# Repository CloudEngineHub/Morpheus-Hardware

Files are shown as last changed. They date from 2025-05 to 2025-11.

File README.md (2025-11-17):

<div align="center">
<h2>Morpheus: A Neural-driven Animatronic Face with<br>
  Hybrid Actuation and Diverse Emotion Control</h2>

  **RSS 2025**
  
<h2>Hardware Design</h2>

**Zongzheng Zhang**<sup>1,2*</sup> · **Jiawen Yang**<sup>1*</sup> · [**Ziqiao Peng**](https://ziqiaopeng.github.io/)<sup>1</sup> ·<br>
**Meng Yang**<sup>4</sup> · [**Jianzhu Ma**](https://majianzhu.com/)<sup>1</sup>, **Lin Cheng**<sup>5</sup> · [**Huazhe Xu**](http://hxu.rocks/)<sup>3</sup> . [**Hang Zhao**](https://hangzhaomit.github.io/)<sup>3</sup> and [**Hao Zhao**](https://sites.google.com/view/fromandto/)<sup>1,2</sup><br>

<sup>1</sup> Institute for AI Industry Research (AIR), Tsinghua University, <sup>2</sup> Beijing Academy of Artificial Intelligence (BAAI),<br>
<sup>3</sup> Institute for Interdisciplinary Information Sciences(IIIS), Tsinghua University, <br>
<sup>4</sup> MGI Tech, Shenzhen, China, <sup>5</sup> Beihang University<br>
<sub>(* indicates equal contribution)</sub><br>
[**RSS official**](https://roboticsconference.org/program/papers/80/) | [**Project Page**](https://jiawenyang-ch.github.io/Morpheus-Hardware-Design/) | [**arXiv**](https://arxiv.org/abs/2507.16645) | [**Hardware**](https://github.com/ZZongzheng0918/Morpheus-Hardware) | [**Software**](https://github.com/ZZongzheng0918/Morpheus-Software)
</div>
<div align="center">
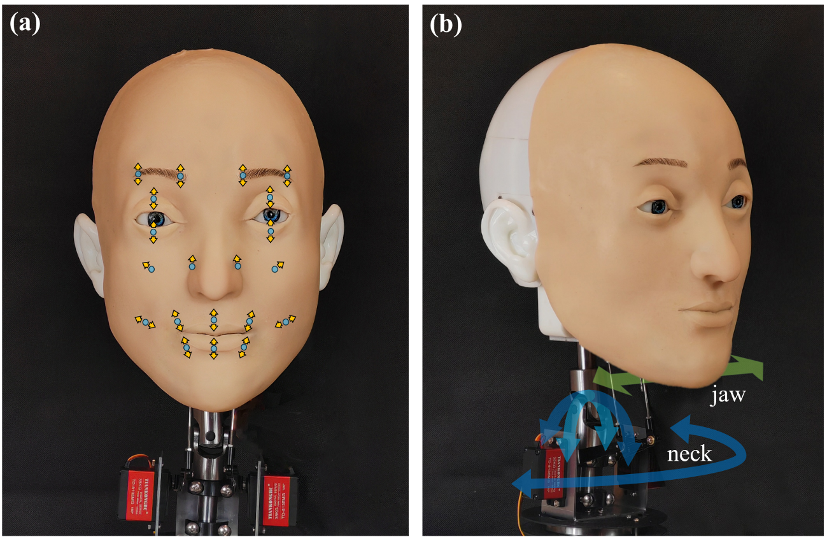
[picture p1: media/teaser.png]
teaser_1
  
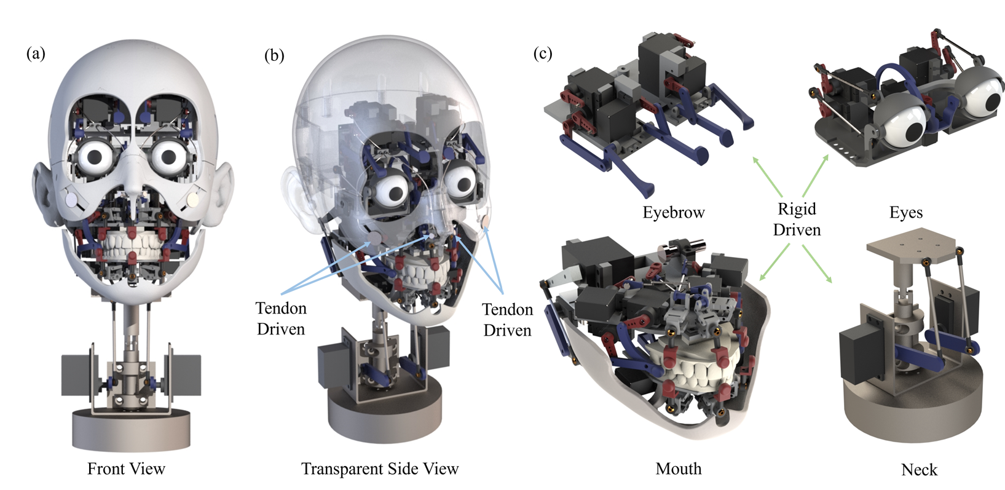
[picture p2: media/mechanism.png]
  
</div>

## Catalog
- [CAD model Download](#cAD_model-Download)
- [Bill of Materials](#bill-of-materials)
- [File content](#file-content)
- [Building Instructions](#building-instructions)
- [Silicone Face](#silicon-face)
- [License and Acknowledgements](#license-and-acknowledgements)
- [Citation](#citation)

## CAD model Download
Due to the large size of the CAD model files, they are hosted on Google Drive instead of being uploaded directly to GitHub. You can download the entire CAD model via the following link:

[Download CAD Model Files](https://drive.google.com/drive/folders/1n12V-EUoFsY6ys1dDMhCXVMRPuU5FeQE?usp=drive_link)

Please ensure you have **SolidWorks 2020 or later** installed to open and edit these files.

## Bill of Materials
All costs are listed in USD.
<table>
  <thead>
    <tr>
      <th>Item</th>
      <th>Quantity</th>
      <th>Cost per Item</th>
      <th>Total Cost</th>
      <th>Note</th>
    </tr>
  </thead>
  <tbody>
    <tr>
      <td>Integy RC GuoHua A0090 9g Metal Gear Digital Micro Servo 6kg</td>
      <td>29</td>
      <td>4.06</td>
      <td>117.74</td>
      <td><a href="https://www.amazon.com/Integy-Model-C30371-GuoHua-Digital/dp/B09CXFTQD5">Purchase Link</a></td>
    </tr>
    <tr>
      <td>RC Spare Part Compatible with KS3518 Rc Car Waterproof Metal Digital Servo High Torque Mechanical Arm Hand Metal Servo Motor</td>
      <td>4</td>
      <td>59.35</td>
      <td>237.4</td>
      <td><a href="https://www.amazon.com/Compatible-KS3518-Waterproof-Digital-Mechanical/dp/B0F5M32RWP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">Purchase Link</a></td>
    </tr>
    <tr>
      <td>10pcs 3-Pin 30cm Servo Extension Cable Cord Female to Male Lead Wire Connector JR for RC Car Airplanes Remote Control-30mm</td>
      <td>33</td>
      <td>7.99</td>
      <td>263.67</td>
      <td><a href="https://www.amazon.com/ACEIRMC-Extension-Connector-Airplanes-Control/dp/B0CQ4QKDF4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">Purchase Link</a></td>
    </tr>
    <tr>
      <td>550PCS M3 Screw Kit</td>
      <td>4</td>
      <td>9.99</td>
      <td>39.96</td>
      <td><a href="https://www.amazon.com/Bemaka-550PCS-Washers-Assortment-Stainless/dp/B0D5CSSYGH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">Purchase Link</a></td>
    </tr>
    <tr>
      <td>Replacement Part For M3 Adjustable Push Rod & Ball Joint Linkage Set Assembly Servo Connecting Rod Stainless Steel For RC Aircraft Boat Part - (Color: 35mm)</td>
      <td>4</td>
      <td>13.99</td>
      <td>55.96</td>
      <td><a href="https://www.amazon.com/dp/B09B3RCDB3/ref=twister_B09B3RLR5K?_encoding=UTF8&th=1">Purchase Link</a></td>
    </tr>
    <tr>
      <td>5/10sets M2 304 Stainless Steel Leather Bag Belt Photo Scrapbook Album Book Post Binding Screw Screw Rivet Metal Screws</td>
      <td>20</td>
      <td>9.66</td>
      <td>193.2</td>
      <td><a href="https://www.amazon.com/YUYUDEHM-Chicago-Assorted-Leather-Bookbinding/dp/B0DGQ5NVW1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">Purchase Link</a></td>
    <tr>
      <td>12Pack Vgoohobby Metal M3 Tie Rod End Ball Holder RC Joint Link Ball Head Holder CW Compatible with HSP Traxxas HPI Axial Redcat Racing 1/10 RC Car Truck Buggy Crawler</td>
      <td>6</td>
      <td>12.99</td>
      <td>77.94</td>
      <td><a href="https://www.amazon.com/12Pack-Vgoohobby-Compatible-Traxxas-Crawler/dp/B0BHF2WG1V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">Purchase Link</a></td>
    </tr>
    <tr>
      <td>2Pcs Aluminum 1.75inch 25T Servo Arm Horn Long Steering Servo Arms Compatible Futaba Savox Xcore HL HSP HD Power Rc Servos for RC Airplanes RC Plane Crawler Car</td>
      <td>1</td>
      <td>9.99</td>
      <td>9.94</td>
      <td><a href="https://www.amazon.com/Aluminum-1-75inch-Steering-Compatible-Airplanes/dp/B0DZBCJXHX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">Purchase Link</a></td>
    </tr>
    <tr>
      <td>LML9B 9mm Linear Rail Mini Bearing Steel Rail Slide Rail+ Slide Block Variety Length (55mm)</td>
      <td>1</td>
      <td>11.62</td>
      <td>11.62</td>
      <td><a href="https://www.amazon.com/LML9B-Linear-Bearing-Variety-Length/dp/B07GQJ9LT8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">Purchase Link</a></td>
    </tr>
    <tr>
      <td>7pcs Realistic Fake Tongue, Magic Tricks Accessories, Halloween Pranking False Tongue Horrific Tongue Prop Tricks Tongue Toys (009)</td>
      <td>1</td>
      <td>8.55</td>
      <td>8.55</td>
      <td><a href="https://www.amazon.com/Realistic-Accessories-Halloween-Pranking-Horrific/dp/B096V99JD5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">Purchase Link</a></td>
    </tr>
    <tr>
      <td>2 Pcs 8mm to 8mm Universal Joint Shaft Coupling with Screws for Motor</td>
      <td>1</td>
      <td>11.99</td>
      <td>11.99</td>
      <td><a href="https://www.amazon.com/Befenybay-Universal-Joint-Coupling-Screws/dp/B07V9NTQLH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">Purchase Link</a></td>
    </tr>
    </tr>
    <tr>
      <td>CanaKit Raspberry Pi 5 Starter Kit PRO - Turbine Black (128GB Edition) (8GB RAM)</td>
      <td>1</td>
      <td>159.99</td>
      <td>159.99</td>
      <td><a href="https://www.amazon.com/CanaKit-Raspberry-Starter-Kit-PRO/dp/B0CRSNCJ6Y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">Purchase Link</a></td>
    </tr>
    <tr>
      <td colspan="3"><b>Total</b></td>
      <td colspan="2"><b>1619.14</b></td>
    </tr>
  </tbody>
</table>

## File content
**Note: This model is compatible with SolidWorks 2020 and later versions.**
```plaintext
CAD_model
├── full_assembly.SLDASM
├── cheek_face_slave_part_mirror.SLDPRT
├── cheek_facial_slave_part_mirror.SLDPRT
├── cheek_line.SLDPRT
├── ks3518.SLDPRT
├── L.SLDPRT
├── nose_line.SLDPRT
├── nose_mirror_line.SLDPRT
├── nose_mirror_slave_part.SLDPRT
├── nose_slave_part.SLDPRT
├── OT.SLDPRT
├── OT_mirror.SLDPRT
├── Raspberry_Pi_(computer_science).SLDPRT
├── shell_back_of_the_head.SLDPRT
├── shell_carapace.SLDPRT
├── shell_Face_Bone_Connectors.SLDPRT
├── shell_Face_Bone_Connectors_mirror.SLDPRT
├── shell_facial_bones.SLDPRT
├── shell_left_ears.SLDPRT
├── shell_right_ears.SLDPRT
├── shell_skin_face.SLDPRT
├── studs.SLDPRT
├── studs_60.SLDPRT
├── "eye"
│   ├── eye.SLDASM
│   ├── eye_Balls_for_head_pulls.SLDPRT
│   ├── eye_bassinet.SLDPRT
│   ├── eye_comb.SLDPRT
│   ├── eye_crank_handle.SLDPRT
│   ├── eye_Eyeball_mounts.SLDPRT
│   └── eye_Eyelid_mounting_stubs.SLDPRT
│   ├── eye_lower_eyelid_of_the_right_eye.SLDPRT
│   ├── eye_lower_eyelid_of_the_right_eye_mirror.SLDPRT
│   ├── eye_m_shaped_board.SLDPRT
│   ├── eye_mounted_version.SLDPRT
│   ├── eye_pupil.SLDPRT
│   ├── eye_Shanks_for_Ball_Tie_Rods.SLDPRT
│   ├── eye_upper_eyelid_of_the_right_eye.SLDPRT
│   ├── eye_upper_eyelid_of_the_right_eye_mirror.SLDPRT
│   ├── eye_y_connector.SLDPRT
├── "eyebrow"
│   ├── EYEBROW.SLDASM
│   ├── eyebrow_brow center motor mounting bracket.SLDPRT
│   ├── eyebrow_brow center pendulum.SLDPRT
│   ├── eyebrow_connected model aircraft regulator.SLDPRT
│   ├── eyebrow_crank v4.SLDPRT
│   ├── eyebrow_eyebrow peak rocker 1.SLDPRT
│   ├── eyebrow_eyebrow peak rocker.SLDPRT
│   ├── eyebrow_GUOHUAA0090.SLDPRT
│   ├── eyebrow_Installation platform.SLDPRT
│   ├── eyebrow_mirror brow center motor mounting bracket.SLDPRT
│   ├── eyebrow_mirror brow center pendulum.SLDPRT
│   ├── eyebrow_mirror eyebrow peak rocker 1.SLDPRT
│   ├── eyebrow_short brow joystick.SLDPRT
├── "mouth"
│   ├── mouth assembly.SLDASM
│   ├── mouth_aluminum rocker arm.SLDPRT
│   ├── mouth_ball of spherical hinge.SLDPRT
│   ├── mouth_baseplate for teeth.SLDPRT
│   ├── mouth_baseplate.SLDPRT
│   ├── mouth_bearing cap.SLDPRT
│   ├── mouth_connector for OT head.SLDPRT
│   ├── mouth_connector for OT head_4mm medium.SLDPRT
│   ├── mouth_connector for OT head_4mmlong.SLDPRT
│   ├── mouth_convex iron wire.SLDPRT
│   ├── mouth_crank.SLDPRT
│   ├── mouth_fourth-generation jaw.SLDPRT
│   ├── mouth_gear.SLDPRT
│   ├── mouth_GUOHUAA0090.SLDPRT
│   ├── mouth_iron wire 30mm.SLDPRT
│   ├── mouth_iron wire_below middle.SLDPRT
│   ├── mouth_iron wire_freedom20mm.SLDPRT
│   ├── mouth_iron wire_freedom30mm.SLDPRT
│   ├── mouth_iron wire_upper middle.SLDPRT
│   ├── mouth_jaw five-bar mechanism_long.SLDPRT
│   ├── mouth_jaw five-bar mechanism_short.SLDPRT
│   ├── mouth_ks3518.SLDPRT
│   ├── mouth_lip connecting rod.SLDPRT
│   ├── mouth_lip six-bar mechanism_4mm crossbar.SLDPRT
│   ├── mouth_lip six-bar mechanism_8mm crossbar.SLDPRT
│   ├── mouth_lower teeth.SLDPRT
│   ├── mouth_metal ball of spherical hinge.SLDPRT
│   ├── mouth_MG90S.SLDPRT
│   ├── mouth_MGN7C_slider.SLDPRT
│   ├── mouth_MGR7_slider rail.SLDPRT
│   ├── mouth_mirror_motor mounting platform for smiling six-bar mechanism.SLDPRT
│   ├── mouth_mirror_oblique crank extension rod.SLDPRT
│   ├── mouth_mirror_smiling five-bar mechanism_below.SLDPRT
│   ├── mouth_motor mounting platform for smiling six-bar mechanism.SLDPRT
│   ├── mouth_mounting platform for upper lip connecting rod.SLDPRT
│   ├── mouth_oblique crank extension rod.SLDPRT
│   ├── mouth_OT head.SLDPRT
│   ├── mouth_perforated crank.SLDPRT
│   ├── mouth_rack.SLDPRT
│   ├── mouth_self-made ball hinge rod for the lower teeth.SLDPRT
│   ├── mouth_shaft flange.SLDPRT
│   ├── mouth_six-bar mechanism_above_short.SLDPRT
│   ├── mouth_six-bar mechanism_below_short.SLDPRT
│   ├── mouth_six-bar mechanism_with spherical hinge.SLDPRT
│   ├── mouth_slide rail mounting plate.SLDPRT
│   ├── mouth_smiling five-bar mechanism_above.SLDPRT
│   ├── mouth_smiling five-bar mechanism_below.SLDPRT
│   ├── mouth_smiling six-bar mechanism_above.SLDPRT
│   ├── mouth_smiling six-bar mechanism_below.SLDPRT
│   ├── mouth_spherical hinge.SLDPRT
│   ├── mouth_threaded pin.SLDPRT
│   ├── mouth_threaded rod of spherical hinge.SLDPRT
│   ├── mouth_tongue connecting rod.SLDPRT
│   ├── mouth_tongue connecting rod_long.SLDPRT
│   ├── mouth_tongue pulling rod.SLDPRT
│   ├── mouth_tongue tray.SLDPRT
│   ├── mouth_upper lip connection point.SLDPRT
│   ├── mouth_upper teeth.SLDPRT
└── "neck"
    ├── neck.SLDASM
    ├── neck_Axis_positioning_tools.SLDPRT
    ├── neck_ball.SLDPRT
    ├── neck_ball_hinge.SLDPRT
    ├── neck_crosshairs.SLDPRT
    ├── neck_extension_arm.SLDPRT
    ├── neck_Installation_of_sheet_metal.SLDPRT
    ├── neck_Parallel_platforms.SLDPRT
    ├── neck_pole.SLDPRT
    ├── neck_principal_axis.SLDPRT
    ├── neck_transition_part.SLDPRT
    ├── neck_universal_joint.SLDPRT
    ├── neck_Upper_shaft.SLDPRT
    └── neck_y_axis_platform.SLDPRT
```

## Building Instructions

### Screw guide

- **Screw A**: M2.5 × 8 mm (Self-tapping) 
- **Screw B**: M3 × 10 mm (Self-tapping) 
- **Screw C**: &#8960;3 (mating screw)  
- **Screw D**: M3  
- **Screw E**: M2 × 10 mm  

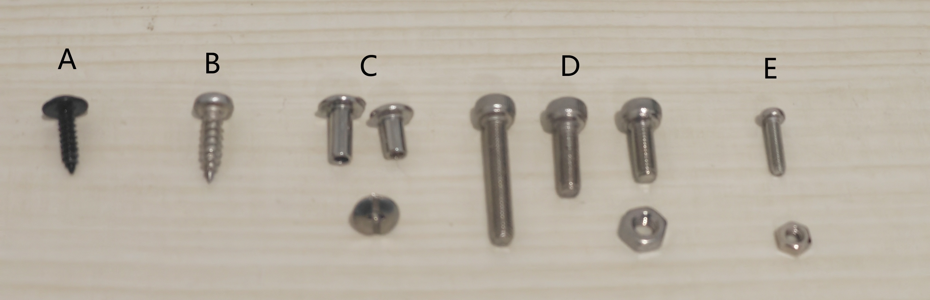
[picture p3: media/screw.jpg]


### Neck module
The *neck_Installation_of_sheet_metal* is installed on the *neck_y_axis_platform* using 4 pairs of screws.

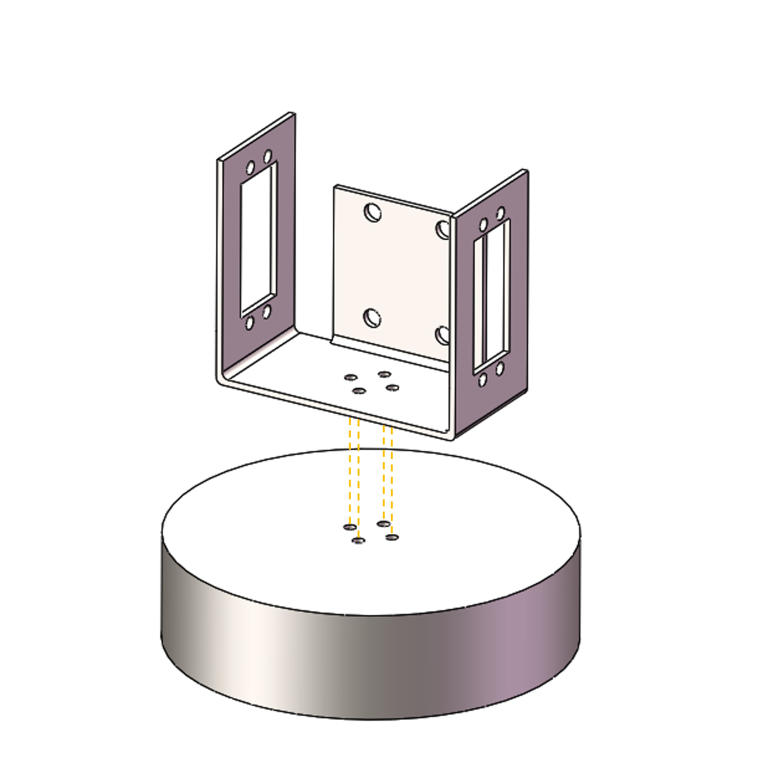
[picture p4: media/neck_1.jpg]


Two *ks3518* servo motors are installed on the *neck_Installation_of_sheet_metal* on both sides.

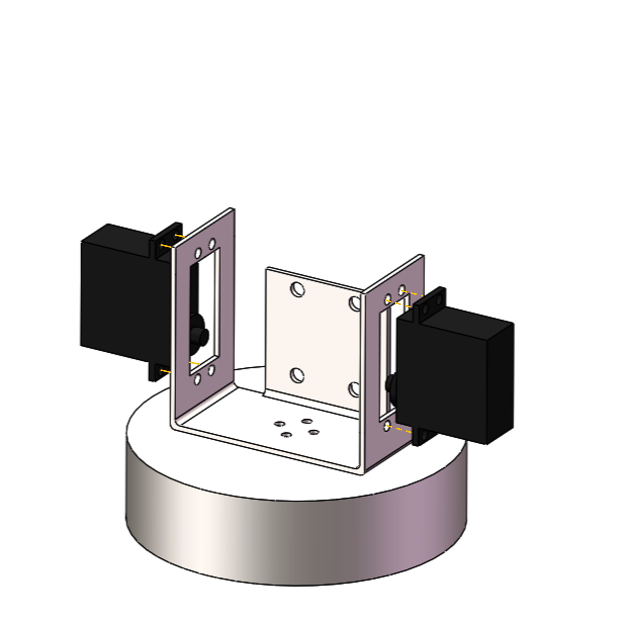
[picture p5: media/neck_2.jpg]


The *neck_extension_arm* is installed on each *ks3518* servo motor to deliver power.

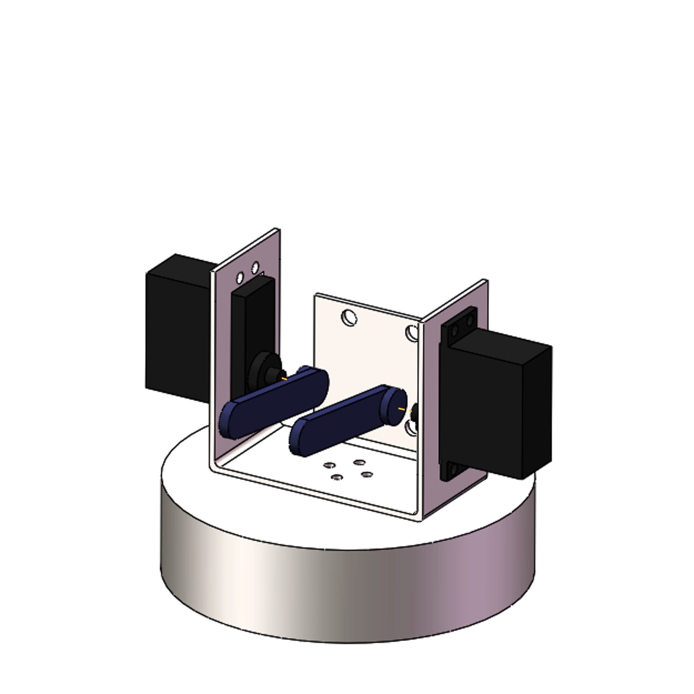
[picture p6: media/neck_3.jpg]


The *neck_principal_axis* is a section of plain shaft which stands on the *neck_Installation_of_sheet_metal*.

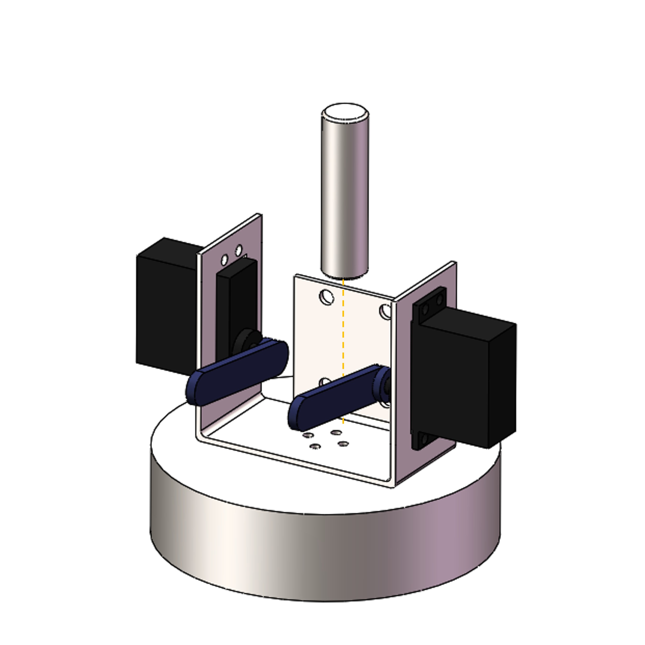
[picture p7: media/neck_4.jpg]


Two *neck_Axis_positioning_tools* are deployed to fix the *neck_principal_axis*.

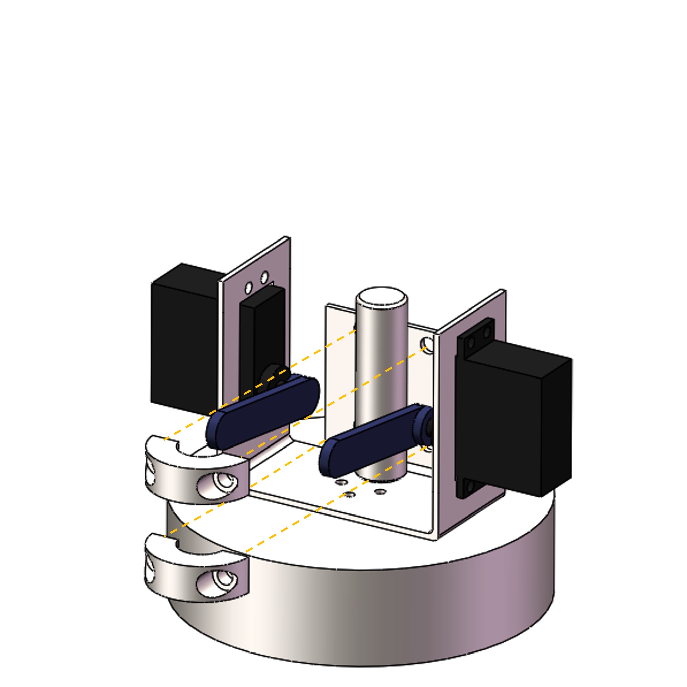
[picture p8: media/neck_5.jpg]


The universal joint is assembled on the upper end of the shaft.

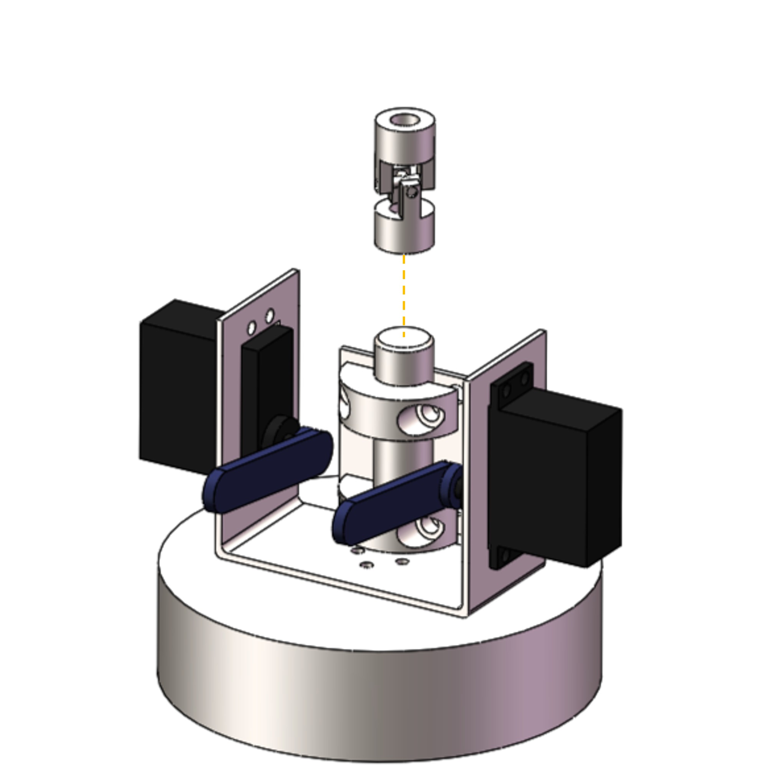
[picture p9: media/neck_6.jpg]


The *neck_Parallel_platforms* is attached with the universal joint with the *neck_Upper_shaft*. 

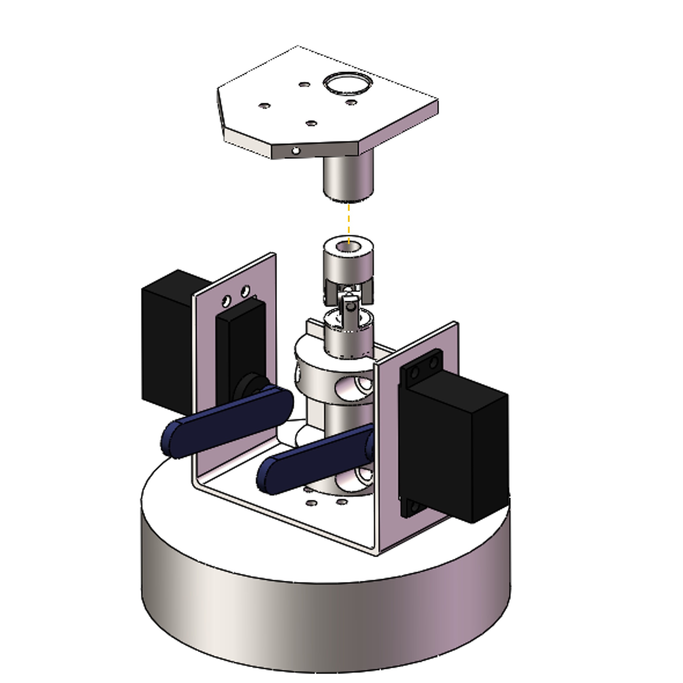
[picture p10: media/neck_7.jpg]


Two rod linkages connect the *neck_Parallel_platforms* and the *neck_extension_arm*s.

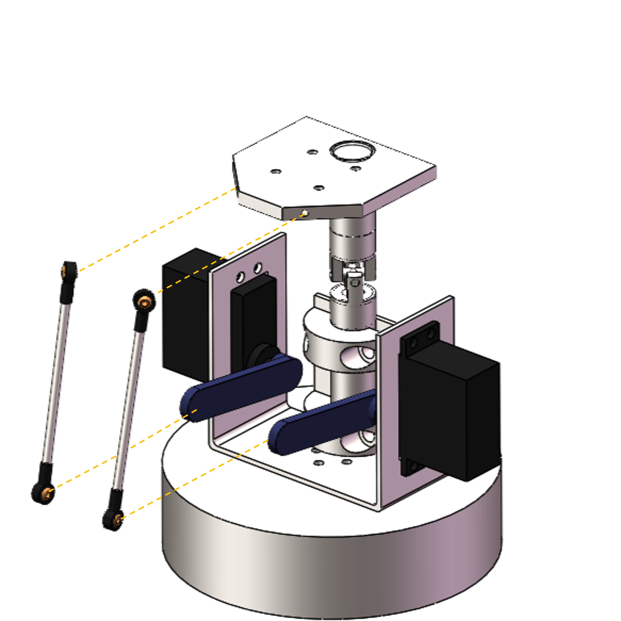
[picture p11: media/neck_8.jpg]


The neck module is completed.

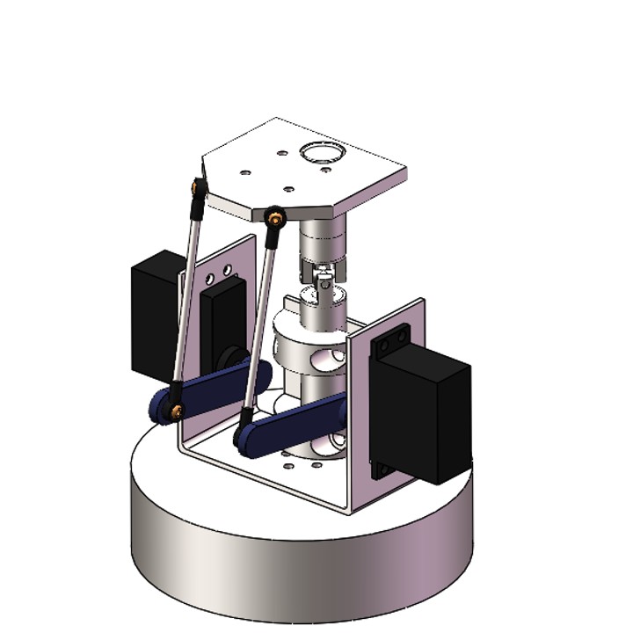
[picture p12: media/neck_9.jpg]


### Eye module

A Guohua servo motor is installed in the middle of the *eye_mounted_version* to control the eyeballs to look vertically. In addition, every servo motor matches a default crank. Therefore, in the following context, servo motor indicates a servo motor and a matching crank if not specified.

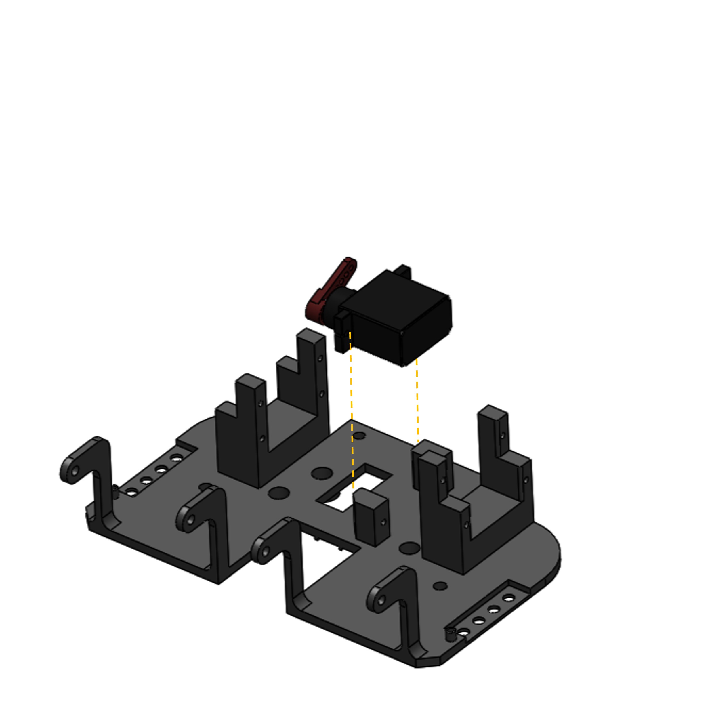
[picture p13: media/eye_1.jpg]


Another Guohua servo motor is install on the *eye_bassinet*, which is then intalled between the eyeballs on the *eye_mounted_version*.

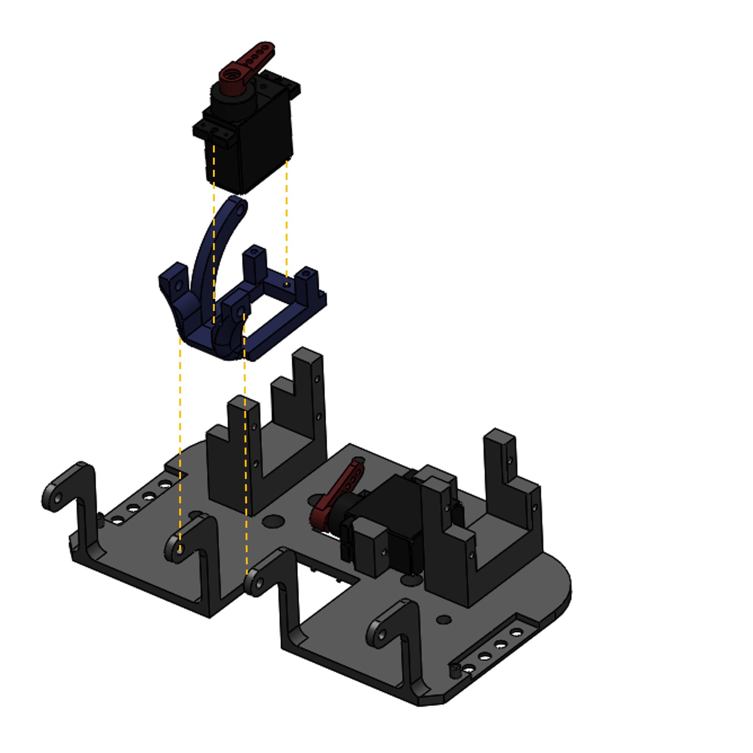
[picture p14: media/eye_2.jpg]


A part called *eye_comb* figuratively is fixed on the *eye_bassinet*. An M-shaped part: *eye_m_shaped_board* is fixed on the crank of the servo. Two Y-shaped parts: *eye_y_connector* connect the two parts mentioned above, forming two identical four-bar mechanisms.

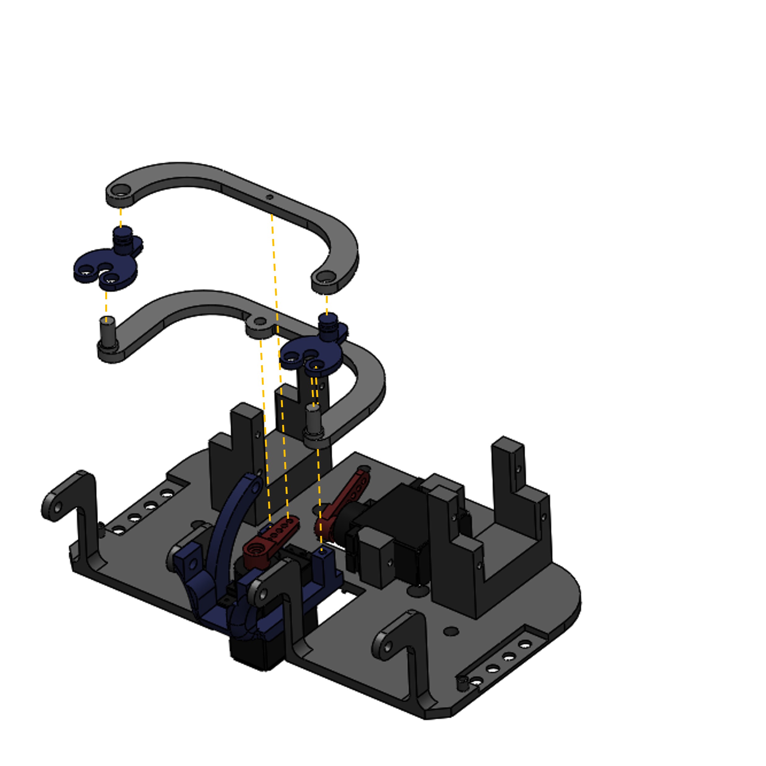
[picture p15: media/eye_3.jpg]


The *eye_Eyeball_mounts* are fixed on the *eye_y_connector*. The micro cameras are fixed on them.

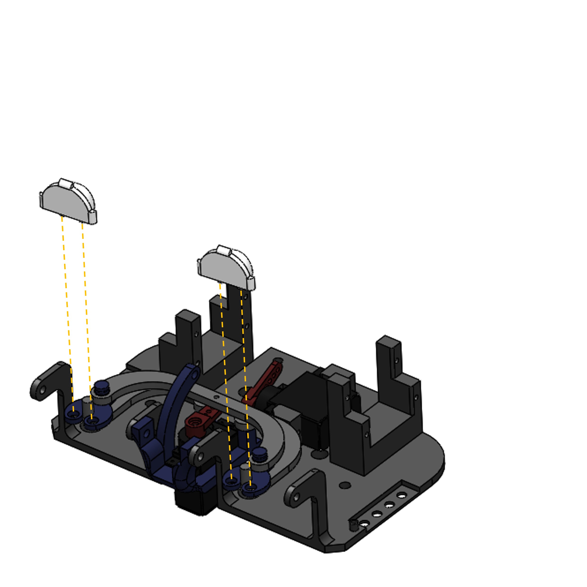
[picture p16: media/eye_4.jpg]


The shell of the eyeballs is mounted on the *eye_Eyeball_mounts*.

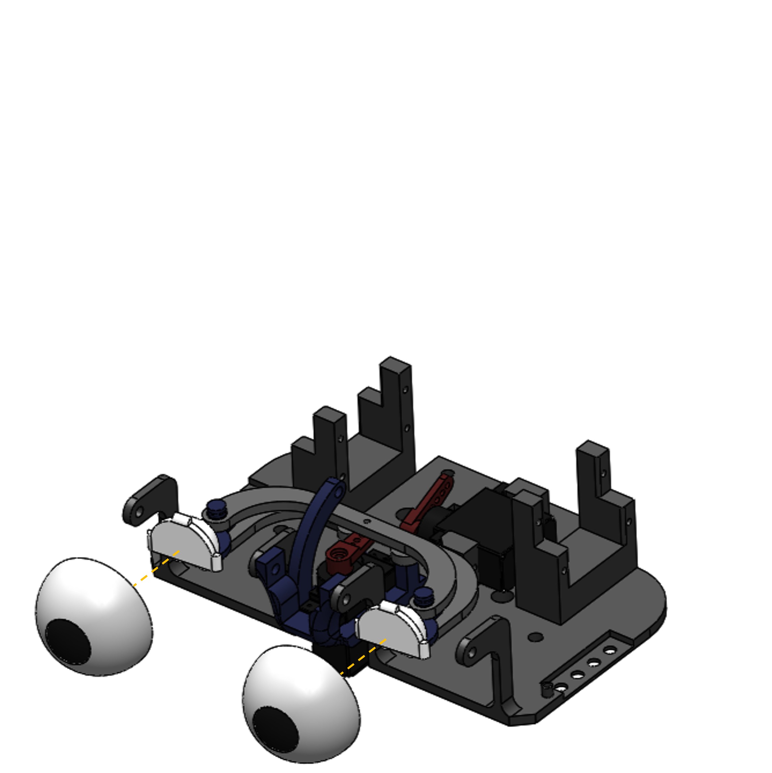
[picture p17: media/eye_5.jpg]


A L-shaped crank connects the crank of the servo motor and the *eye_bassinet*, forming a new four-bar mechanism.

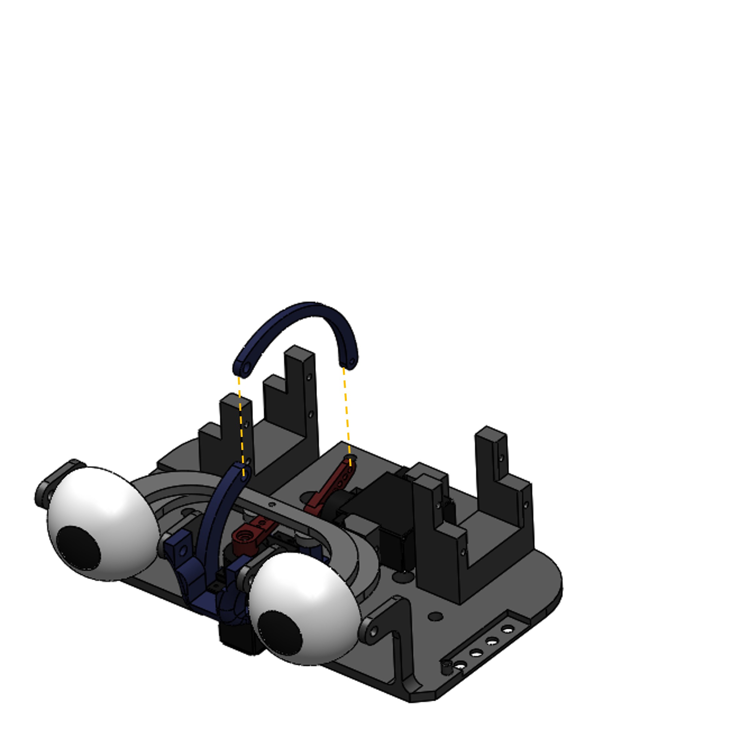
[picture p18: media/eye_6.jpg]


The four eyelids are then assenmbled around the eyeball.

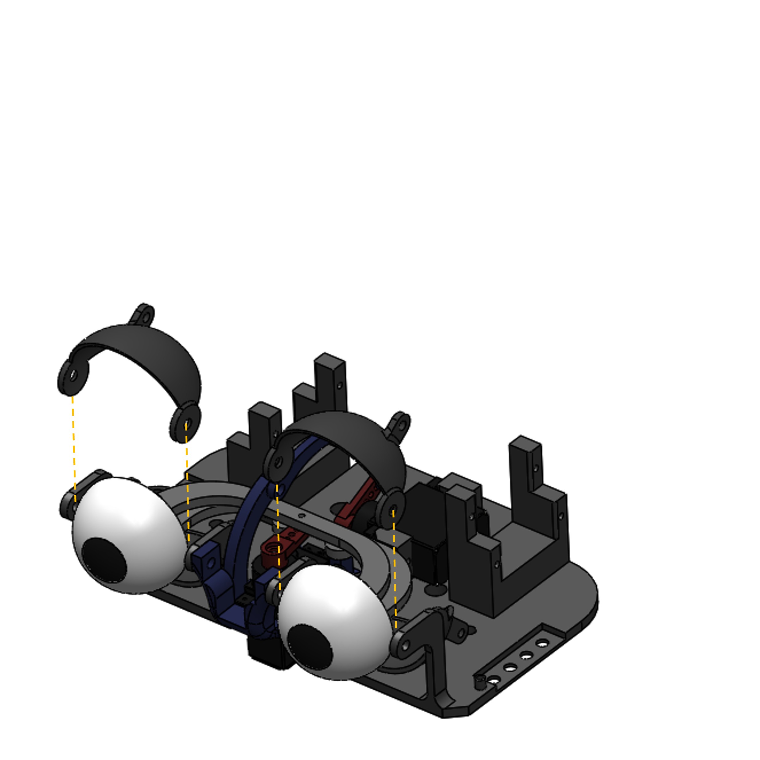
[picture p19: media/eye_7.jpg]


Four servo motors controlling the eyelids are mounted on the *eye_mounted_version*.

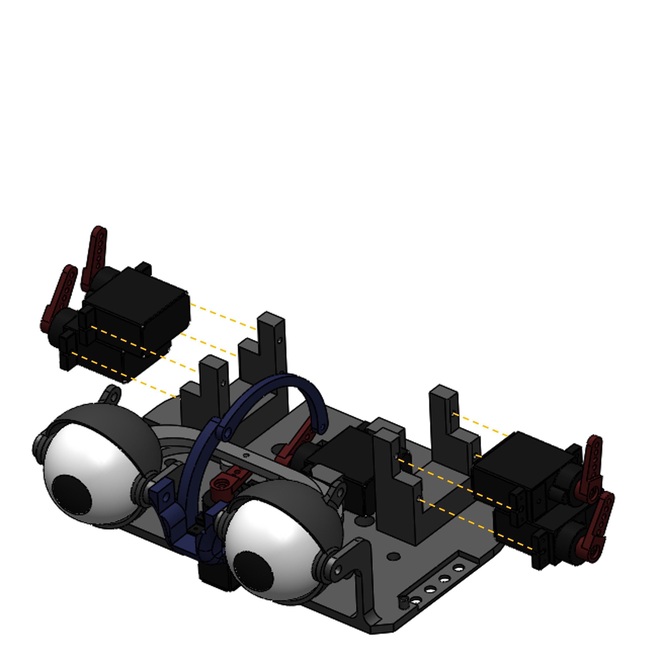
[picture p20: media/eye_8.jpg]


The *eye_upper_eyelid_of_the_right_eye* and *eye_upper_eyelid_of_the_left_eye* are driven by two rod linkages.

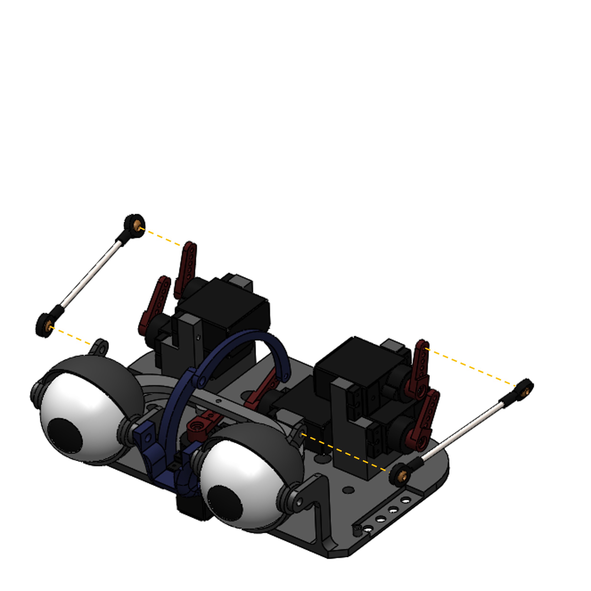
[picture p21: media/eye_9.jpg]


Ditto for the lower eyelids.

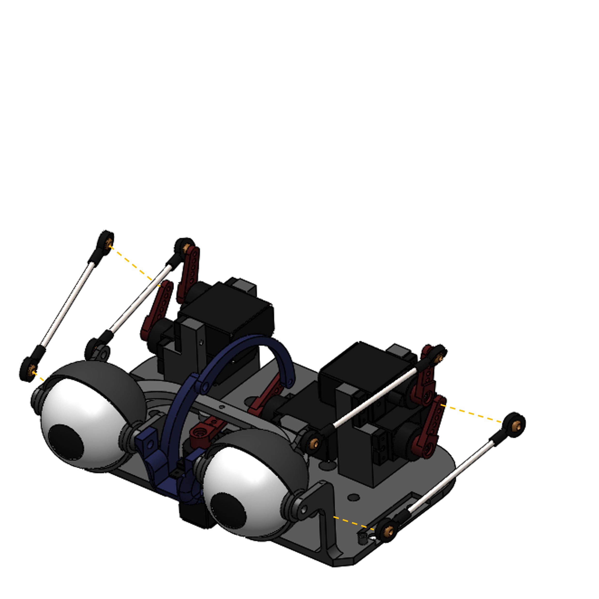
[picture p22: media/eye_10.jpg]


The eye module is completed.

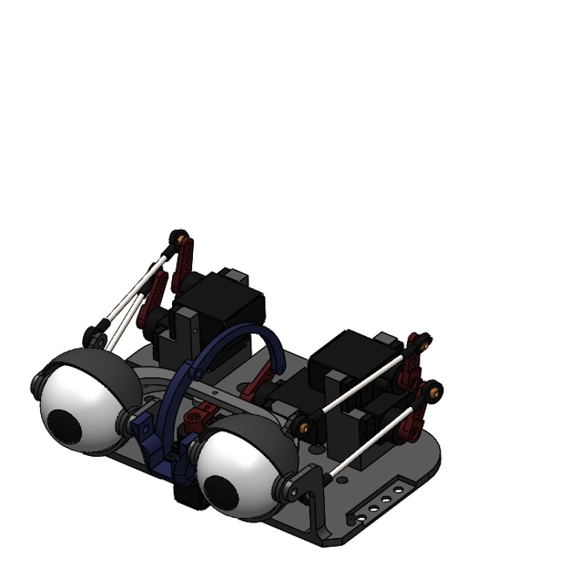
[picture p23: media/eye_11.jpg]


### Eyebrow module

The two *eye_brow_center_motor_mounting_brackets* are mirror-symmetric which servo motors, *eyebrow_brow_center_pendelums*, and *eyebrow_short_brow_joysticks* are install on. The crank of the servo motor, the *eyebrow_short_brow_joysticks* (rod), and *eyebrow_brow_center_pendelums* (rocker) constitutes a four-bar mechanism.

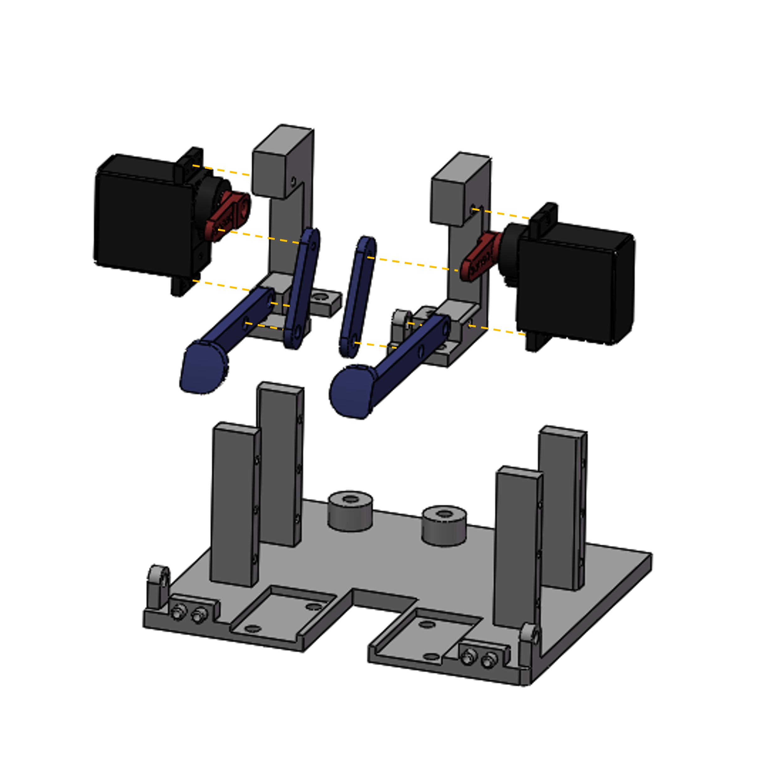
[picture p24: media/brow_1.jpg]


The two *eye_brow_center_motor_mounting_brackets* are installed on the *eyebrow_Installation_platform*.

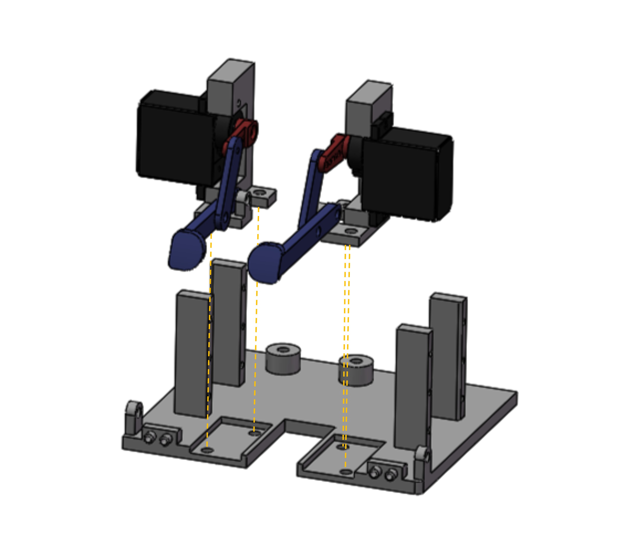
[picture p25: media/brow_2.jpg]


Six servo motors are installed on the back of the *eyebrow_Installation_platform* staggeredly.

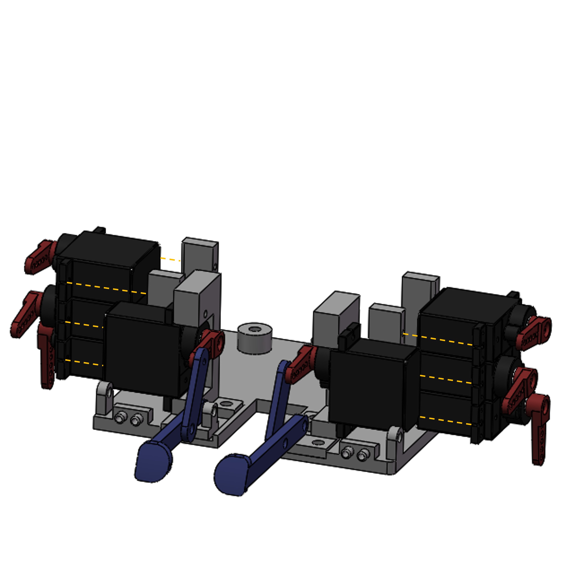
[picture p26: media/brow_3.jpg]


The *eyebrow_eyebrow_peak_rockers* are installed on the side.

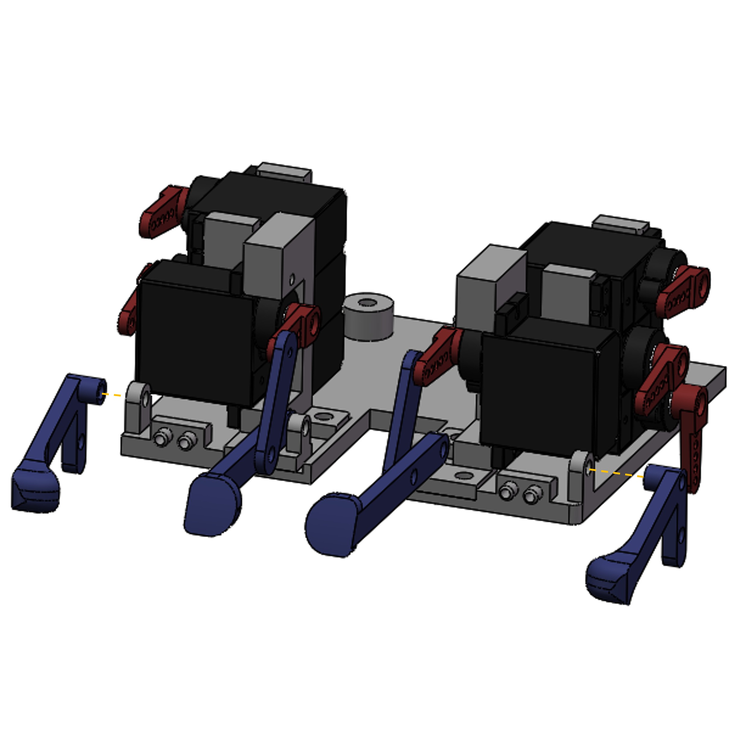
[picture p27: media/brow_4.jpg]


Another rod along with the crank of the servo motor installed at the bottom forms another four-bar mechanism.

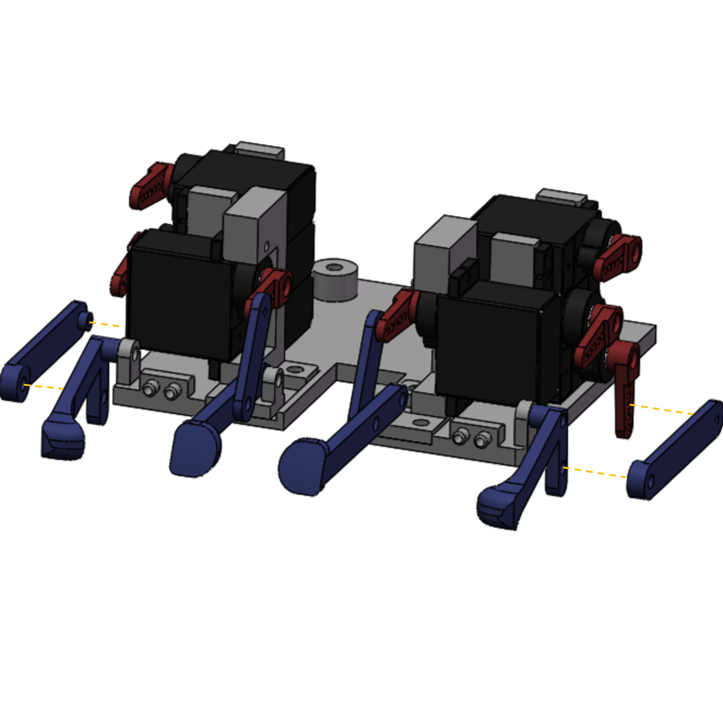
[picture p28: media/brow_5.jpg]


The eyebrow module is complete.

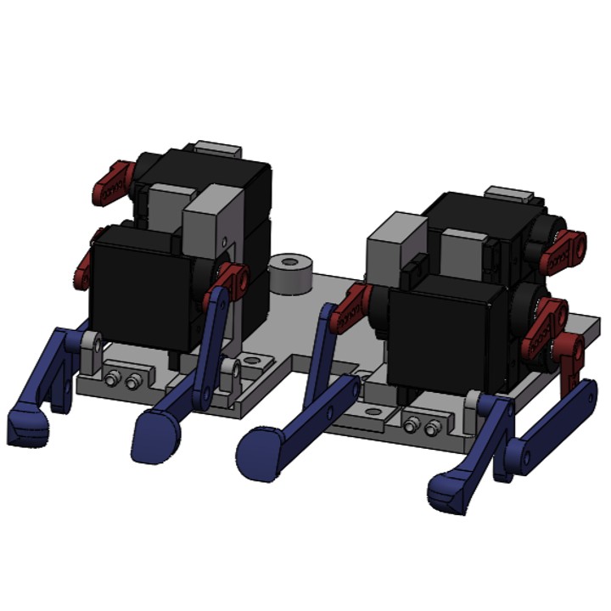
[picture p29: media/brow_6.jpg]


### Mouth module

Two *mouth_motor_mounting_platform_for_smiling_six-bar_mechanisms* are installed on the *mouth_baseplate*.

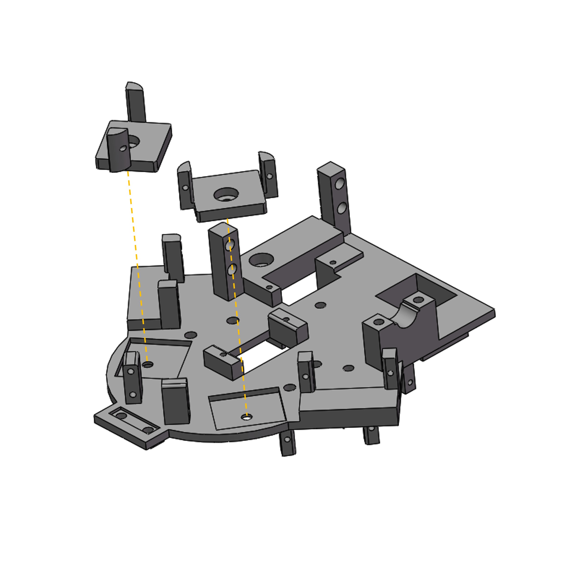
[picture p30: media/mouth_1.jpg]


Two rods and two servo motors form the five-bar mechanism. And the latter are installed on the *mouth_motor_mounting_platform_for_smiling_six-bar_mechanisms*.

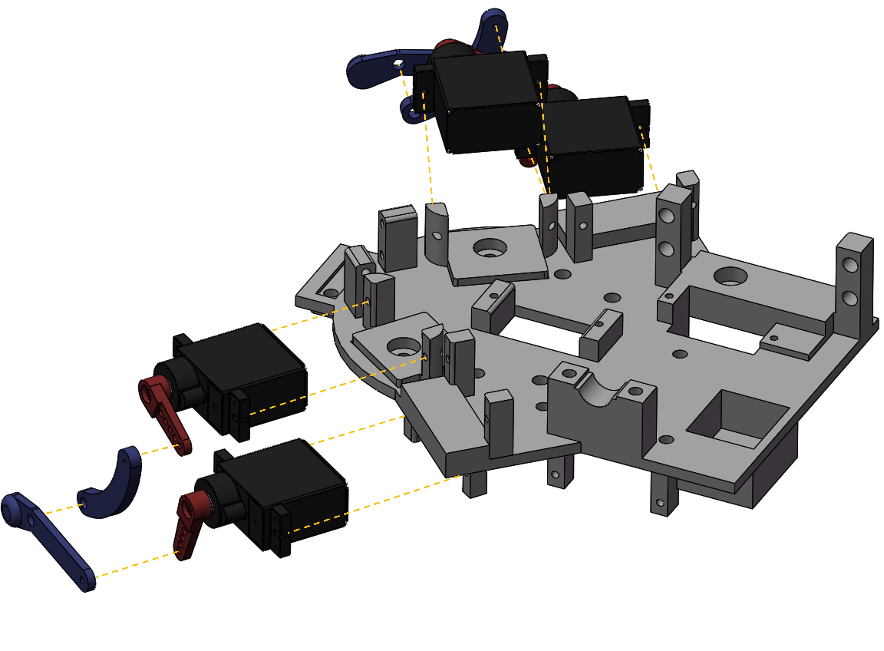
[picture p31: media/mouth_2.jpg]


Three servo motors are then installed on the *mouth_baseplate* to control the upper lips.

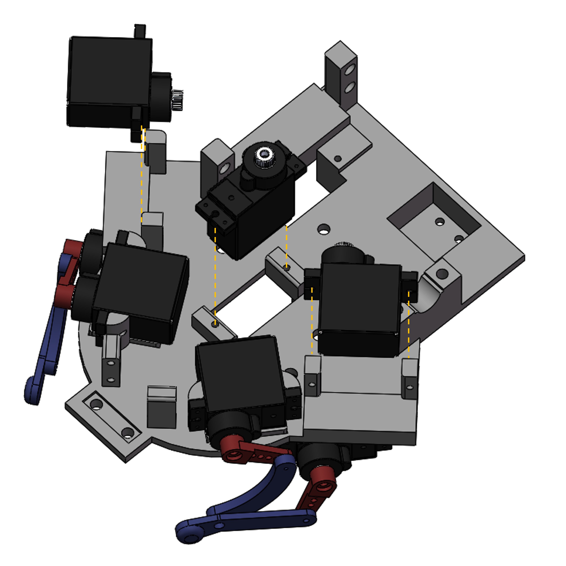
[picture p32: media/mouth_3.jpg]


At the front of the *mouth_baseplate*, there are two mounting structures，which is used to install the three of the six rods of the six-bar mechanism used to control the lips.

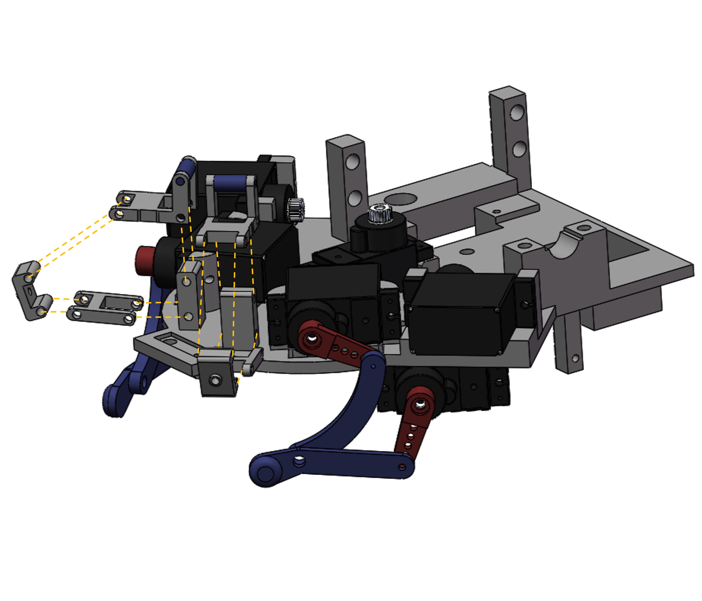
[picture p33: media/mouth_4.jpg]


An addtional mounting part is installed in the middle.

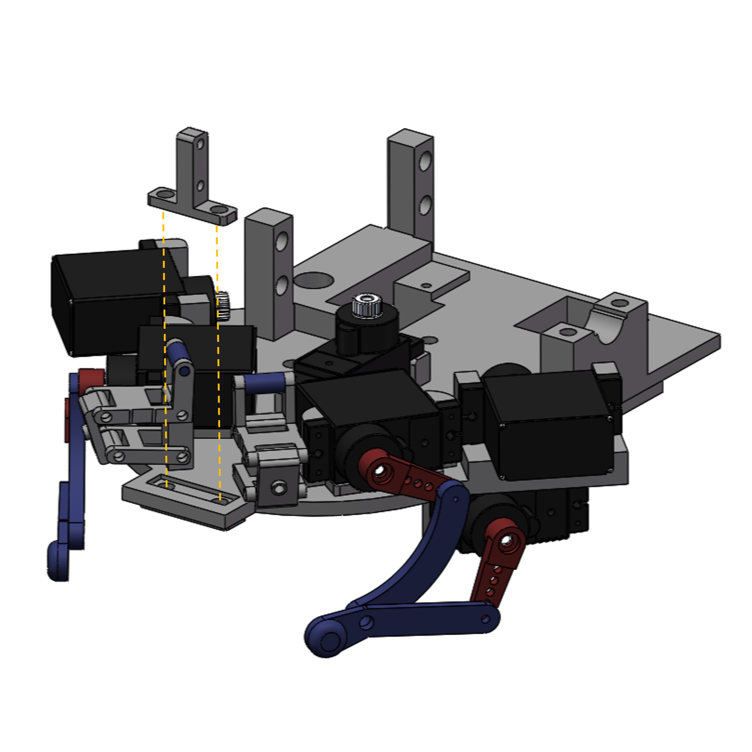
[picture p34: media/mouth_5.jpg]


This part has the same funciton as the mounting structure.

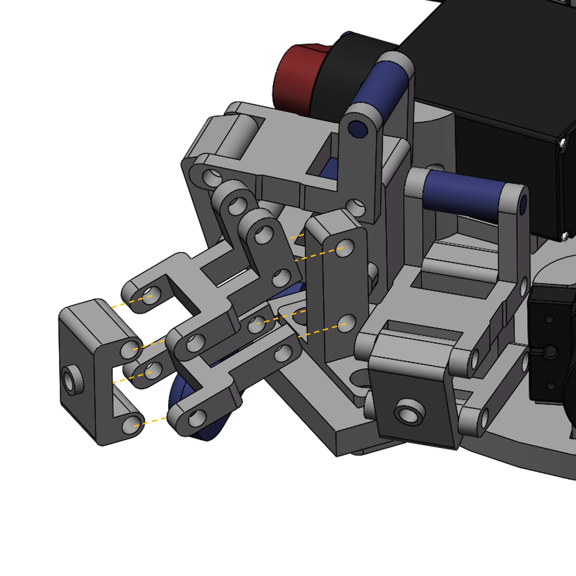
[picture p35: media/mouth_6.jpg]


Then, three adaptively deformed iron wires are used to connect the crank to the rods. The 2mm-dimeter wires are manually adjusted and equipped with two open terminals at both ends. To connect the wires with the cranks and rods, the suggested method is to use 2mm-dimeter mating screws and bushing whose inner dimeter is 2mm, outter dimeter is 4mm.

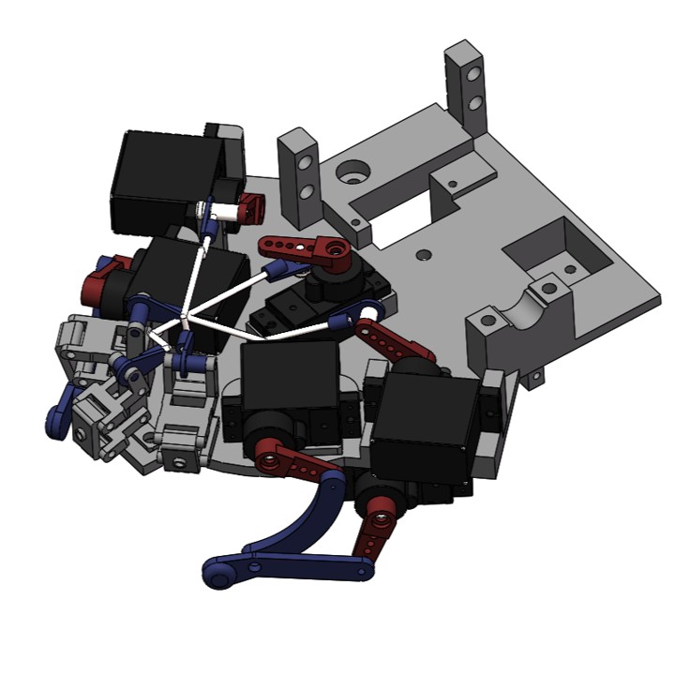
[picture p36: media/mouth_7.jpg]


One servo motor is installed from the bottom up, with a gear between the motor and the crank.

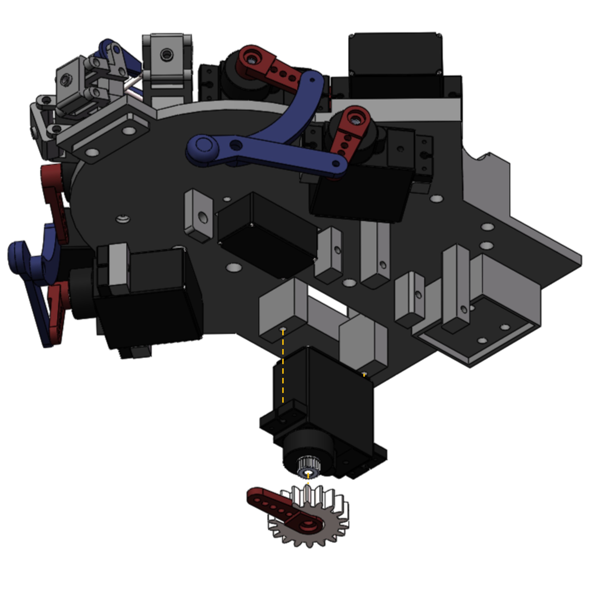
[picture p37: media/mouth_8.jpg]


For the *mouth_slide_rail_mounting_plate*, a MGR7 slider rail is installed on it.

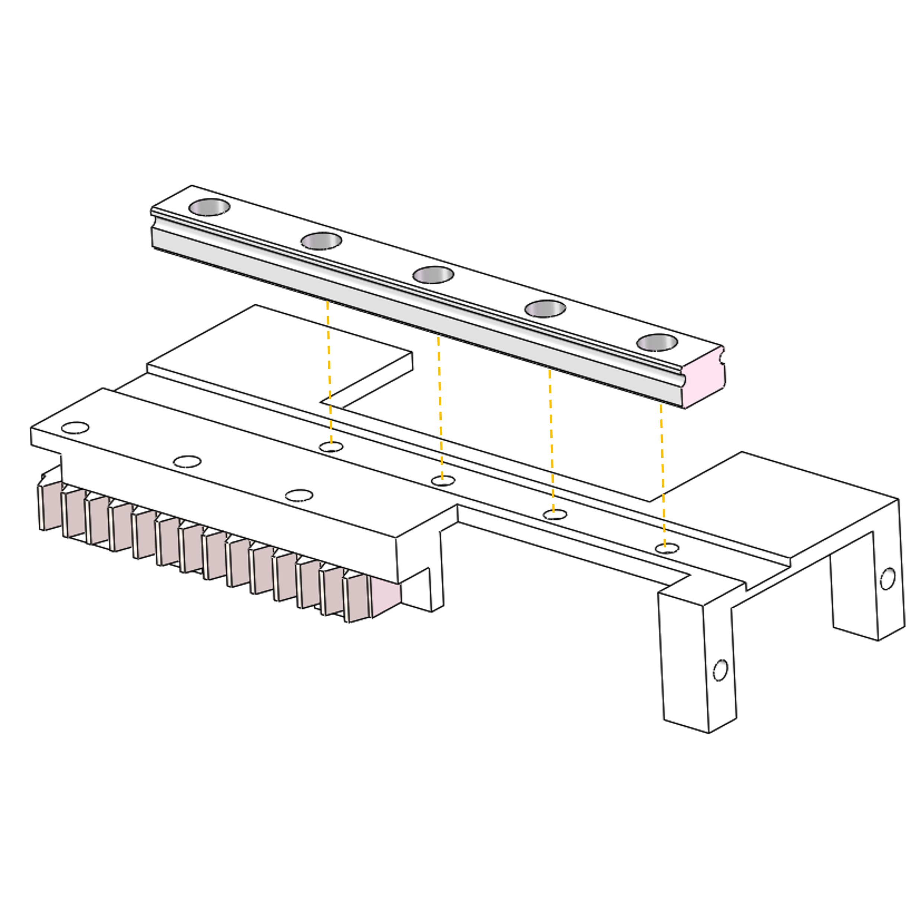
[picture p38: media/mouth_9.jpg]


Two servo motors are installed on the side to control the motion of the jaw opening and closing.

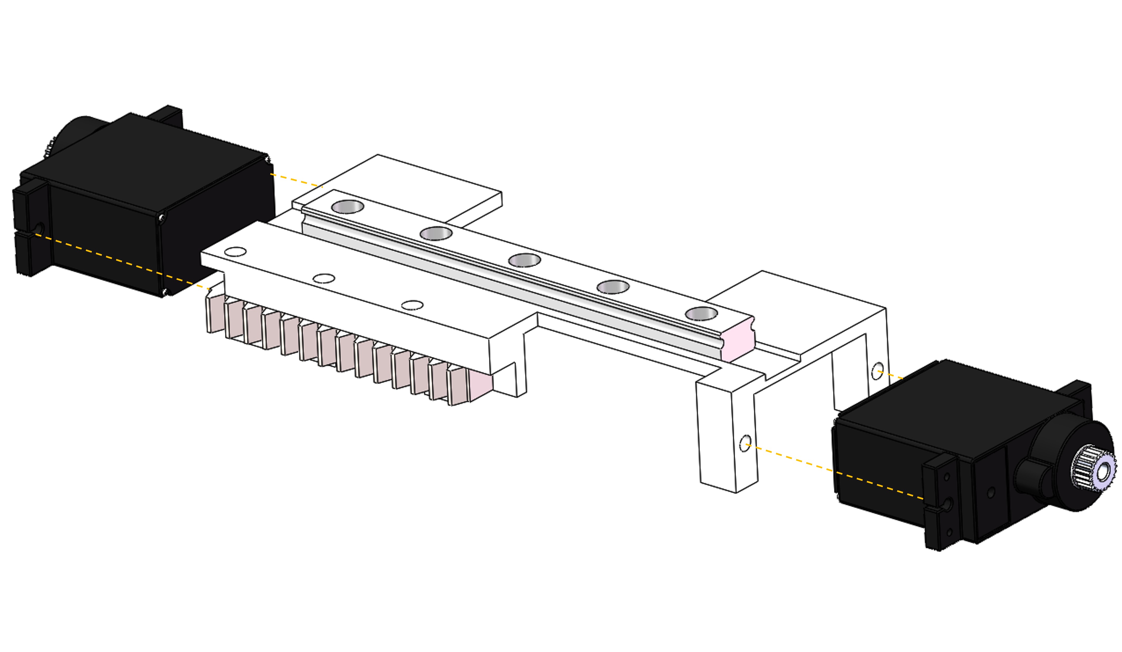
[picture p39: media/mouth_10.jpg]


The matching slider is installed on the bottom of *mouth_motor_mounting_platform_for_smiling_six-bar_mechanisms*.

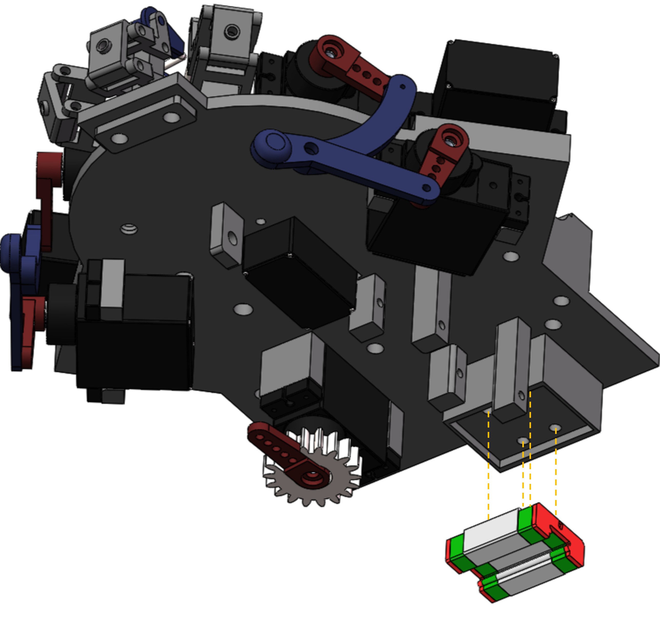
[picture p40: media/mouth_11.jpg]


teaser_1

Two servo motors are installed next to the aforemetioned motor.

teaser_1

The *mouth_tongue_connecting_rod_long* and *mouth_perforated_crank* with their matching motor and crank form a four-bar mechanism. The *mouth_tongue_connecting_rod* and *mouth_tongue_pulling_rod* with their matching motor and crank form another four-bar mechanism. Two four-bar mechanisms are connected in parallel.

teaser_1

On the *mouth_baseplate_for_teeth* are the three servo motors controlling the lower lip.

teaser_1

The mechanism at the front is the same as that of the upper lip.

teaser_1

Two *mouth_oblique_crank_extension_rods* are fixed on the cranks on both sides. At the end of that extension rods are the *mouth_threaded_pin* used to install *mouth_metal_ball_of_spherical_hinges*.

teaser_1

Different from the upper lip, another *mouth_threaded_pin* with ball of spherical hinge is install on the *mouth_six-bar_mechanism_with_spherical_hinge*.

teaser_1

One rod with ball hinge on both sides connects the *mouth_six-bar_mechanism_with_spherical_hinge* and the extended rod.

teaser_1

The *mouth_baseplate_for_teeth* is fixed on the jaw.

teaser_1

The lower teeth is then installed on the jaw.

teaser_1

The upper teeth is installed on the bottom of the *mouth_baseplate*.

teaser_1

The *mouth_shaft_flange* is placed on the half-hole of the *mouth_baseplate*. The cap is installed on the half-hole to locate the shaft. A crank of 32mm is connected with the motor on the *mouth_slide_rail_mounting_plate*, and the other end connected with jaw. A long rod connects the *mouth_shaft_flange* and jaw, forming a five-bar mechanism.

teaser_1

On the other side of the jaw, a large servo motor ks3518 is installed on the *mouth_baseplate*, whose matching crank is 38mm long.

teaser_1

A rod connects the longer crank and the jaw. 

teaser_1

To give more freedom around the control points on the lip, spherical hinges are used.

teaser_1

The mouth module is complete.

teaser_1

### Modules' assembly

A *neck_transition_part* is used to connect the neck module and the mouth module.

teaser_1

Four studs of 60mm are used as the connector.

teaser_1

teaser_1

Four studs of 30mm are used as the connector between the mouth module and the eye module.

teaser_1

teaser_1

Three studs of 60mm are used as the connector between the eye module and the eyebrow module.

teaser_1

teaser_1

*Shell_Face_Bones* are used to connect the eye module and facial mask.

teaser_1

The ears are connected with the facial mask. The back of the head is located by two ears. 

teaser_1

The skull is then mounted on the back of the head.

teaser_1

The lines go through the holes designed on the eye and eyebrow module.

teaser_1

## Silicon Face
To optimize expression accuracy and realism, especially in tendon-driven regions, we carefully tested silicone materials. We used A00-30 silicone, known for its skin-like softness, and adopted a 3D-printed mold solution for efficient iteration. The silicone was mixed (1:1 ratio), degassed in a vacuum chamber (-0.1 MPa, 5-10 min), poured into the mold, and cured at 25°C for 4-8 hours, followed by a 24-hour resting period to enhance performance. Material tension was adjusted by thickness (2mm, 2.5mm, 4mm, 5mm), with the eye area thinned to 2mm to prevent localized buildup at the eyelid. For tendon-driven sections, experiments determined that 4mm skin provided the best balance between visibility and actuation capability.

teaser_1

## License and Acknowledgements
This source code is licensed under the Apache 2.0 liscence found in the LICENSE file in the root directory of this repository.

## Citation
If you find this project useful, feel free to cite our work!
<div style="display:flex;">
<div>

```bibtex
@article{zhang2025morpheus,
  title={Morpheus: A Neural-driven Animatronic Face with Hybrid Actuation and Diverse Emotion Control},
  author={Zhang, Zongzheng and Yang, Jiawen and Peng, Ziqiao and Yang, Meng and Ma, Jianzhu and Cheng, Lin and Xu, Huazhe and Zhao, Hang and Zhao, Hao},
  journal={arXiv preprint arXiv:2507.16645},
  year={2025}
}
```

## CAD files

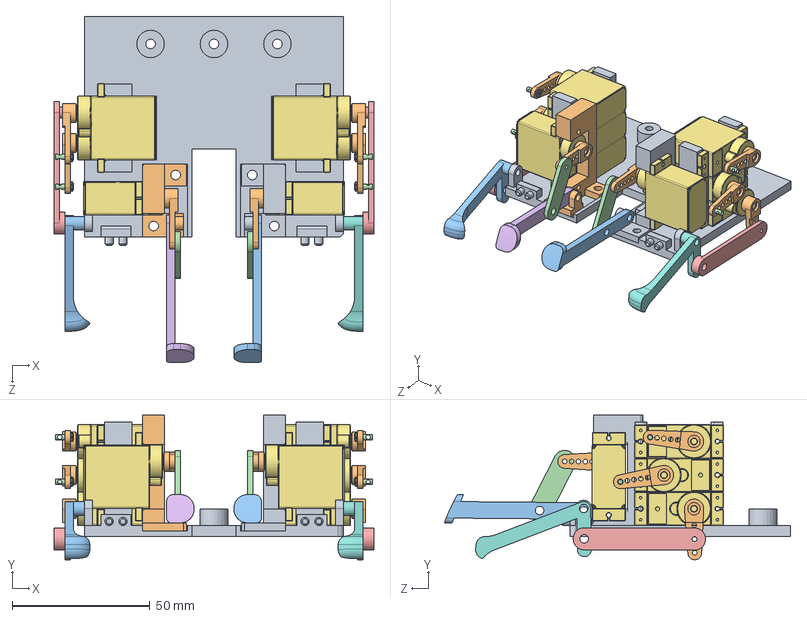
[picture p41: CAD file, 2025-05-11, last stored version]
eyebrow/EYEBROW.SLDASM
116.0 x 52.4 x 125.5 mm
eyebrow_Installation platform
eyebrow_crank v4 x 8
eyebrow_brow center pendulum
eyebrow_short brow joystick x 2
eyebrow_eyebrow peak rocker x 2
eyebrow_mirror brow center pendulum
eyebrow_GUOHUAA0090 x 8
eyebrow_eyebrow peak rocker 1
eyebrow_brow center motor mounting bracket
eyebrow_mirror brow center motor mounting bracket
eyebrow_mirror eyebrow peak rocker 1
eyebrow_connected model aircraft regulator x 4
hex thin nuts-grades ab-chamfered gb x 4

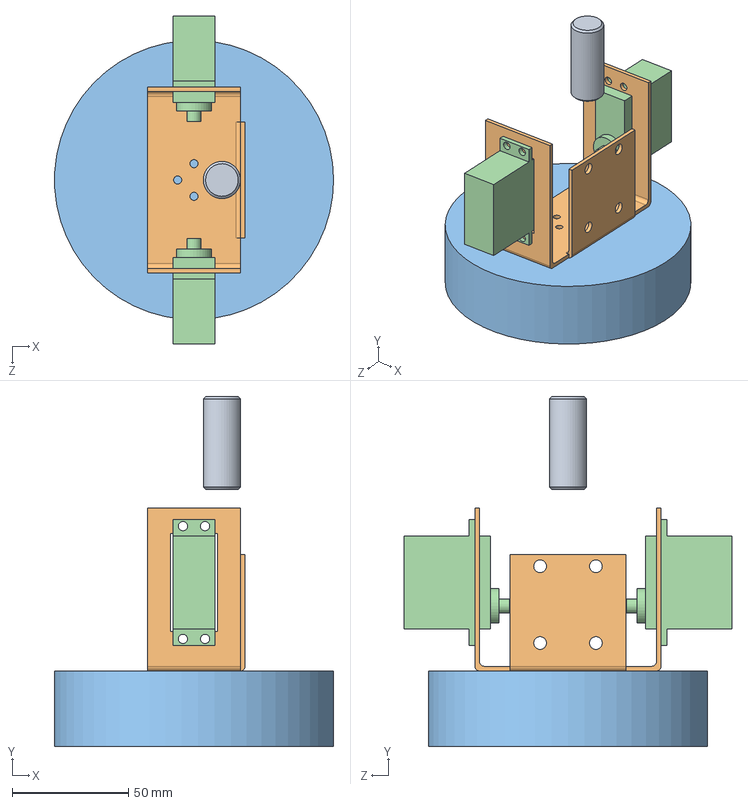
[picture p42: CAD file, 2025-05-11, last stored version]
neck/neck.SLDASM
120.0 x 150.5 x 141.0 mm
neck_y_axis_platform
ks3518 x 2
neck_Installation_of_sheet_metal
neck_Upper_shaft

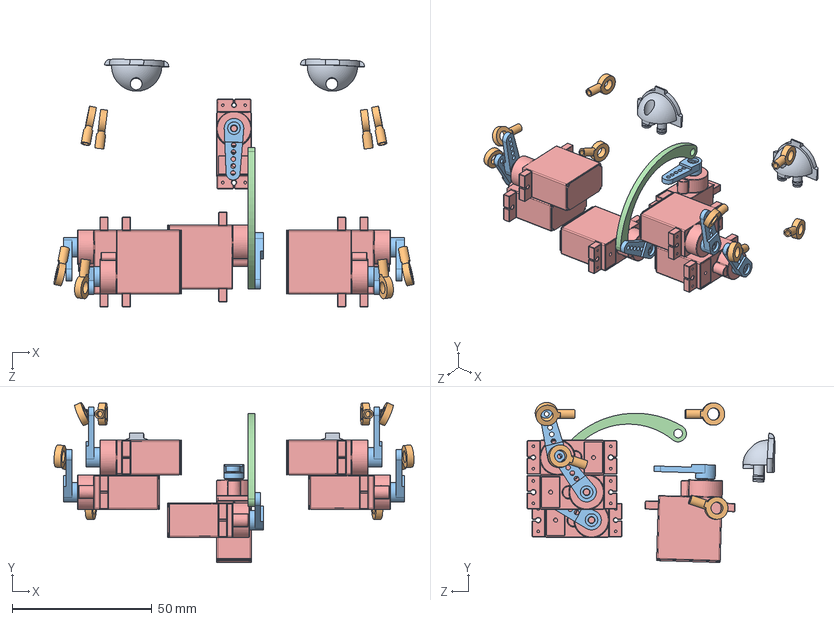
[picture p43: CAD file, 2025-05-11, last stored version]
eye/eye.SLDASM
128.8 x 57.3 x 88.6 mm
eye_crank_handle x 6
eye_Shanks_for_Ball_Tie_Rods x 10
L
MG90S x 6
eye_Eyeball_mounts x 2

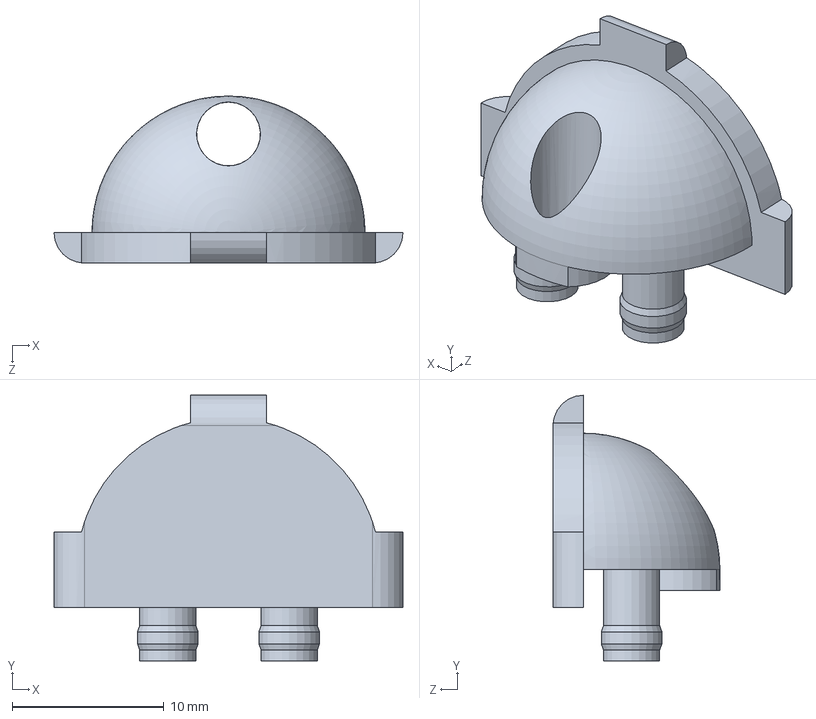
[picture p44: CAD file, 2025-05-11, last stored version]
eye/eye_Eyeball_mounts.SLDPRT
23.0 x 17.5 x 11.0 mm

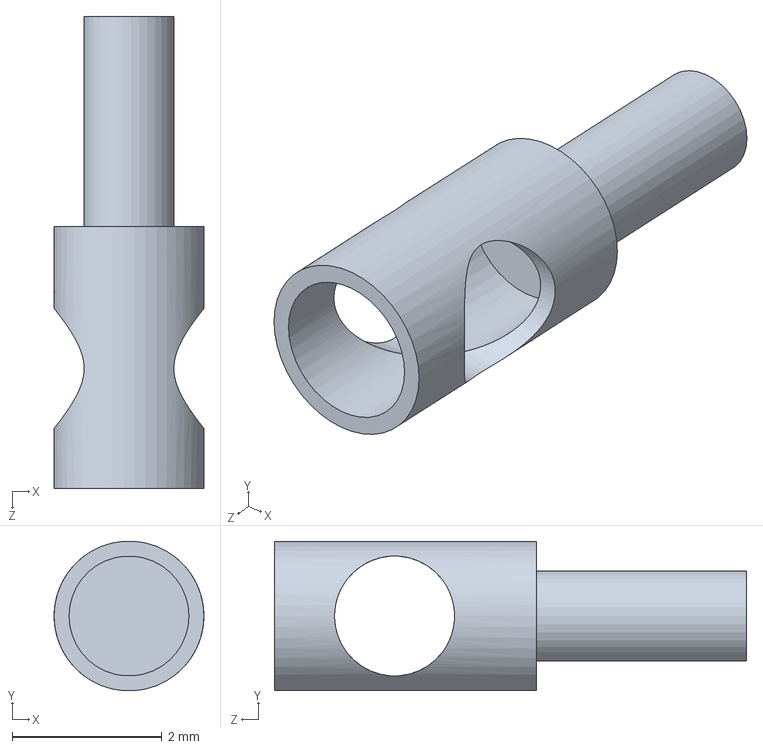
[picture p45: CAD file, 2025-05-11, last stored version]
eyebrow/eyebrow_connected model aircraft regulator.SLDPRT
2.00 x 1.99 x 6.30 mm

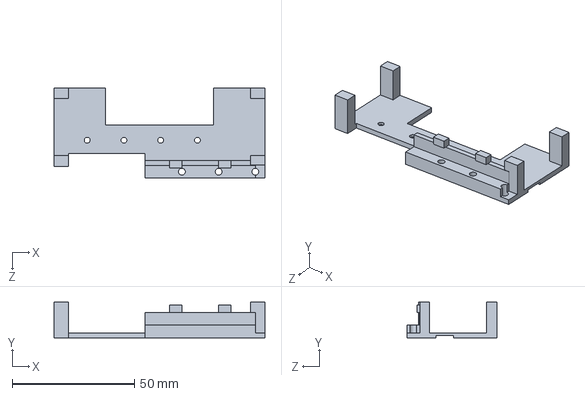
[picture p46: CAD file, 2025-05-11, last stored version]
mouth/mouth_slide rail mounting plate.SLDPRT
86.2 x 14.5 x 36.6 mm

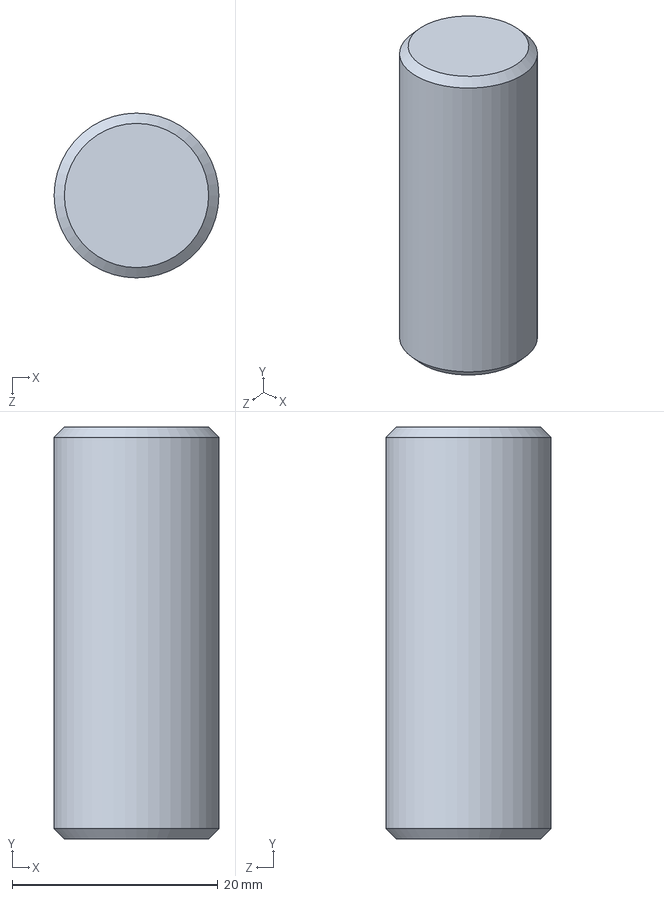
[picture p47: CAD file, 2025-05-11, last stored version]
neck/neck_Upper_shaft.SLDPRT
16.0 x 40.0 x 16.0 mm

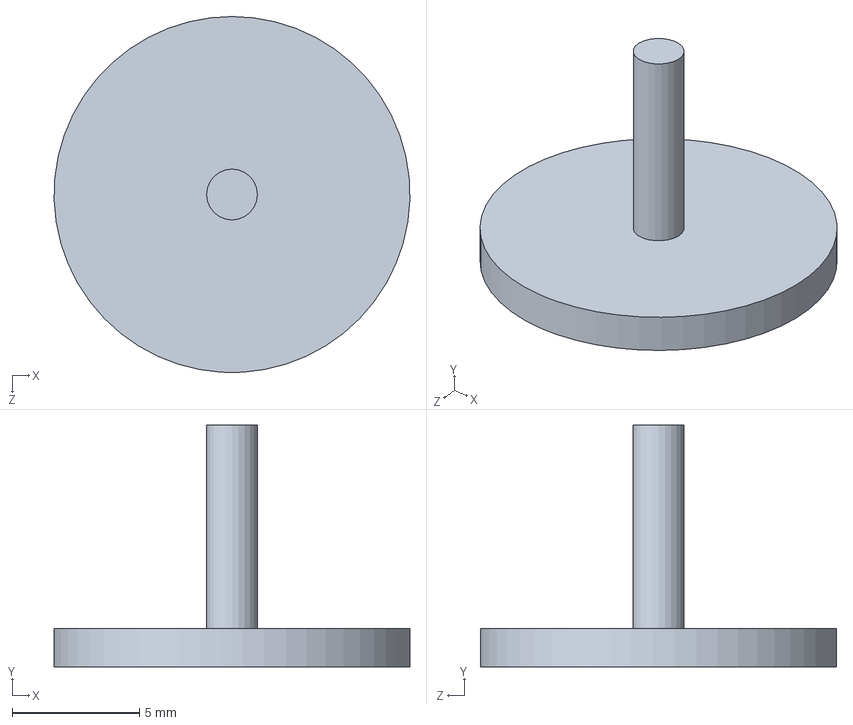
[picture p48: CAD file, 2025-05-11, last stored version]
CAD model/cheek_face_slave_part_mirror.SLDPRT
14.0 x 9.50 x 14.0 mm

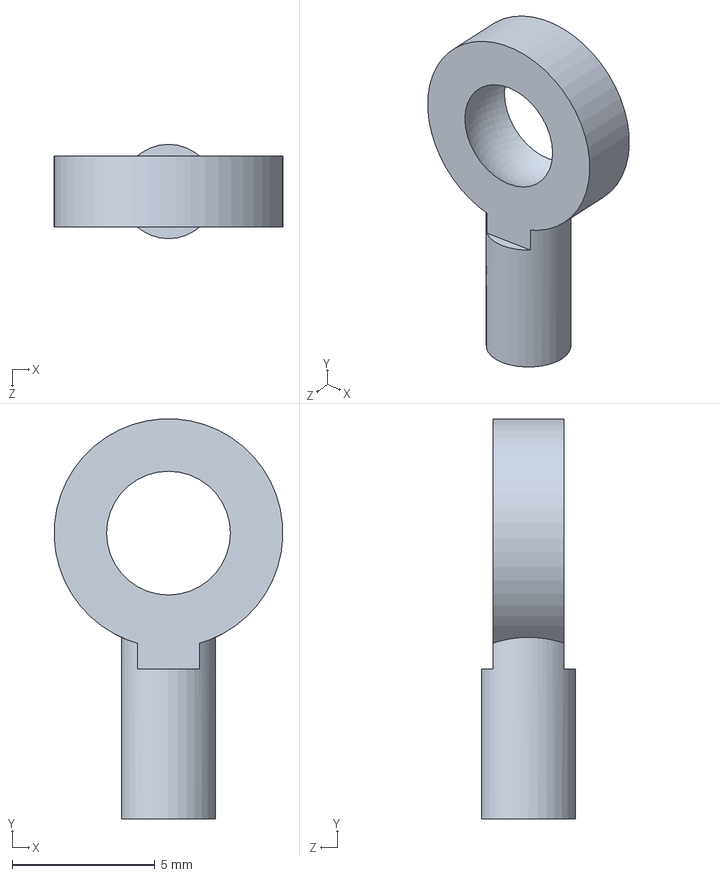
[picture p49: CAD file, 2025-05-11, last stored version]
eye/eye_Shanks_for_Ball_Tie_Rods.SLDPRT
7.99 x 14.0 x 3.30 mm

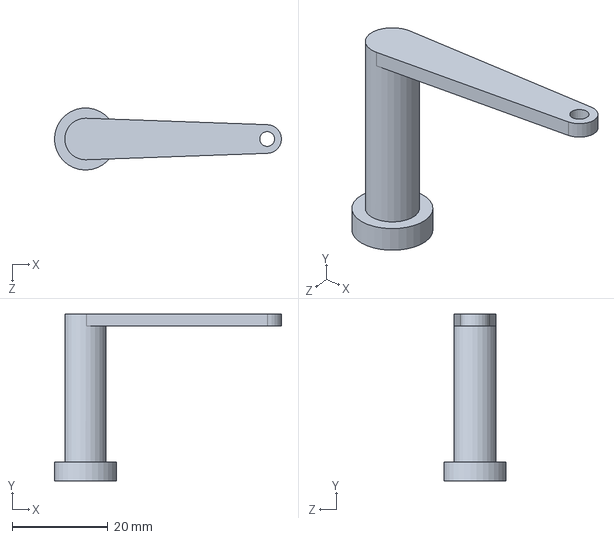
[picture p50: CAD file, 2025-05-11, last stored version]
mouth/mouth_shaft flange.SLDPRT
47.5 x 34.9 x 13.0 mm

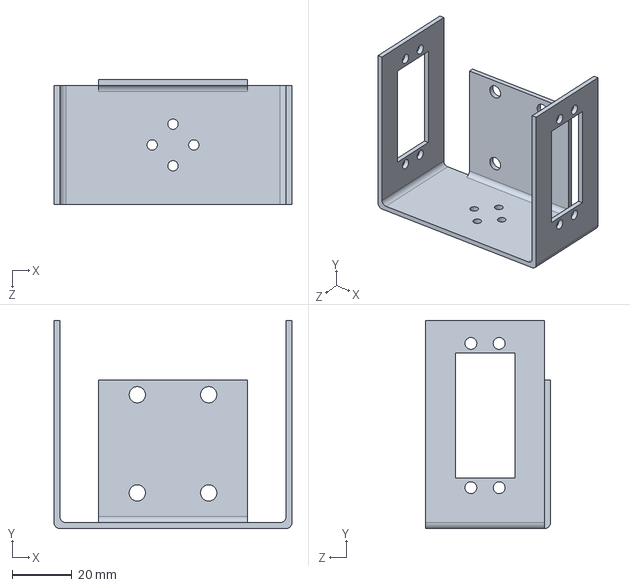
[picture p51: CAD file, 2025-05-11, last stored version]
neck/neck_Installation_of_sheet_metal.SLDPRT
80.0 x 70.0 x 42.0 mm

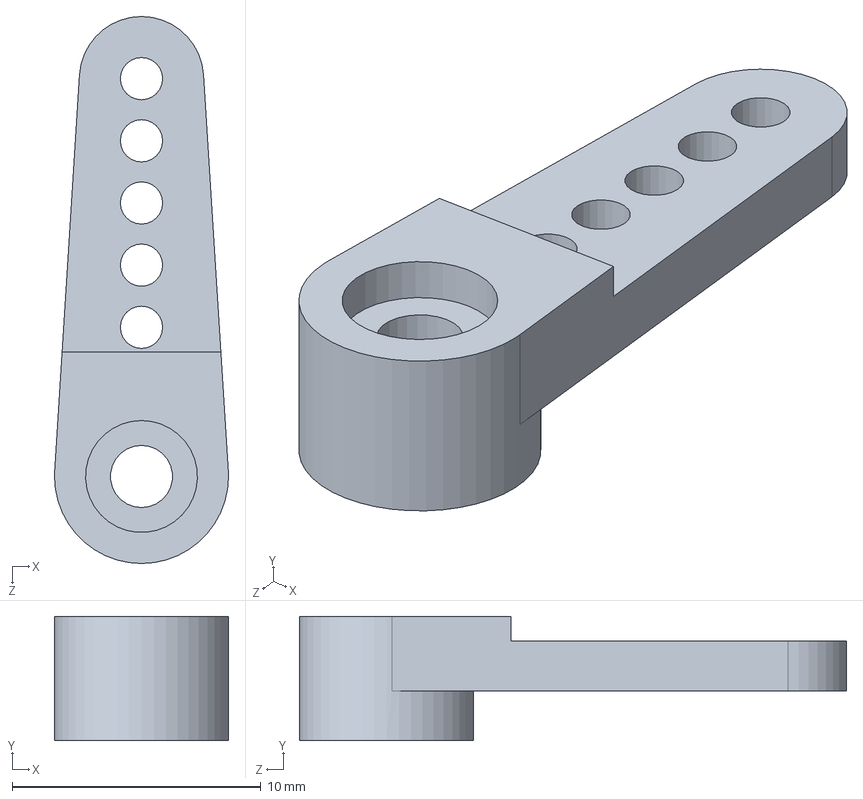
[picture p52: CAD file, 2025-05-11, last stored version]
eye/eye_crank_handle.SLDPRT
7.00 x 5.00 x 22.0 mm

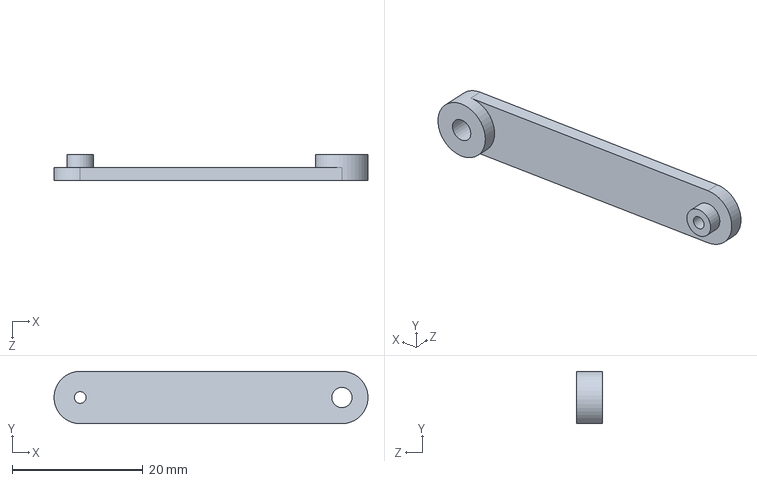
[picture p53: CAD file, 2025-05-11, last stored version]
eyebrow/eyebrow_eyebrow peak rocker.SLDPRT
48.0 x 8.00 x 4.00 mm

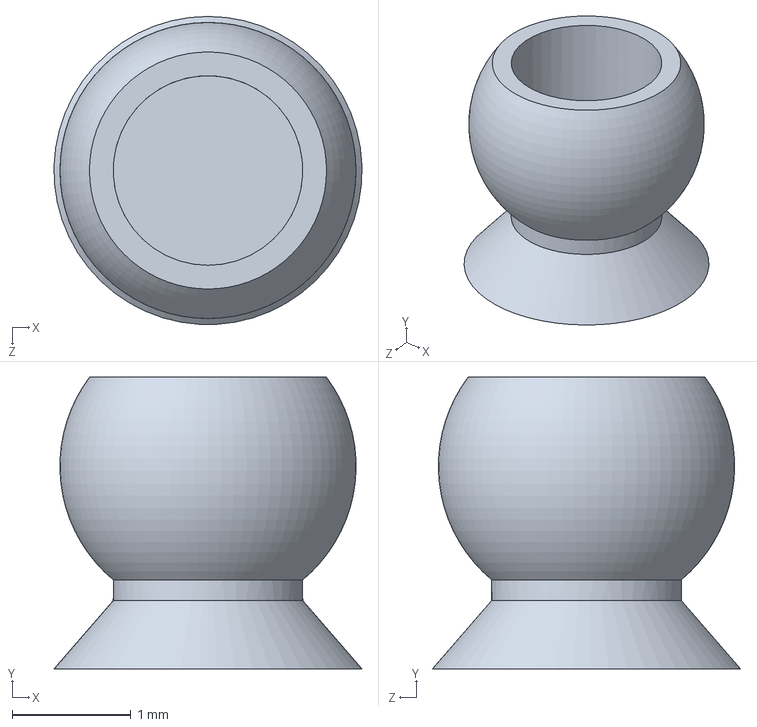
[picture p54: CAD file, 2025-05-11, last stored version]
mouth/mouth_metal ball of spherical hinge.SLDPRT
2.60 x 2.46 x 2.60 mm

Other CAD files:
CAD model/cheek_line_mirror.SLDPRT
CAD model/cheek_facial_slave_part_mirror.SLDPRT
neck/neck_y_axis_platform.SLDPRT
CAD model/cheek_line.SLDPRT
eye/eye_Balls_for_head_pulls.SLDPRT
eye/eye_Eyelid_mounting_stubs.SLDPRT
eye/eye_bassinet.SLDPRT
eye/eye_camera_eyeball.SLDPRT
eye/eye_comb.SLDPRT
eye/eye_lower_eyelid_of_the_right_eye.SLDPRT
eye/eye_lower_eyelid_of_the_right_eye_mirror.SLDPRT
eye/eye_m_shaped_board.SLDPRT
eye/eye_mounted_version.SLDPRT
eye/eye_pupil.SLDPRT
eye/eye_upper_eyelid_of_the_right_eye.SLDPRT
eye/eye_upper_eyelid_of_the_right_eye_mirror.SLDPRT
eye/eye_y_connector.SLDPRT
eyebrow/eyebrow_GUOHUAA0090.SLDPRT
eyebrow/eyebrow_Installation platform.SLDPRT
eyebrow/eyebrow_brow center motor mounting bracket.SLDPRT
eyebrow/eyebrow_brow center pendulum.SLDPRT
eyebrow/eyebrow_eyebrow peak rocker 1.SLDPRT
eyebrow/eyebrow_mirror brow center motor mounting bracket.SLDPRT
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
